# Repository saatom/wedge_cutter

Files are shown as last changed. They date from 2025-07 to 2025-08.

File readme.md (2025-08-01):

# readme
Created by Wyatt Richards <wr1701@proton.me>

beta branch

Made during my time working at Great Land Window.

This is a dispenser for _TREMCO POLYSHIM II_ window wedge (specifically the 0.160" size). It is designed to work with a NEMA 23 closed-loop stepper motor with approximately 3.0 Nm of maximum output torque. Bearings are standard 802 22mm OD/ 8mm ID ones with a smaller bearing on the giullotine assembly specified as having 7mm OD / 3mm ID.

Oversized holes are for machine screw heat-set inserts (M3 and M4 sizes) with three pockets for M5 nuts on the motor housing assembly.

Electrical diagram(s) for this machine are not provided but are pretty straight forward. It is designed to use 20 vdc input from Dewalt brand batteries, which is split into three different voltages and are as follows:
* 20 to 35 vdc step up module for 35 vdc input to the stepper driver
* 7 vdc regulator for servo power
* 5 vdc for Raspberry PI Pico input (note that the RPI has an internal voltage regulator that brings it down to 3.3 vdc, thus all logic and LEDs are running on 3.3 volts and not 5)

Pin configurations are designed for ease of assembly and maintenance and are hard-coded into the .ino file, which is compiled using the standard arduino-cli package for Linux and uploaded manually to the RPI.

Please consult the instruction manual with questions, otherwise you can email me at the aforementioned address.



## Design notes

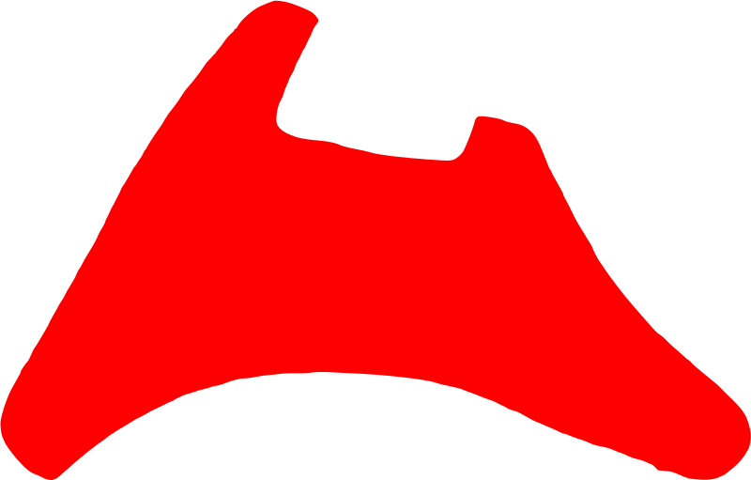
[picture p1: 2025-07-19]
Cutter_Profile2.png

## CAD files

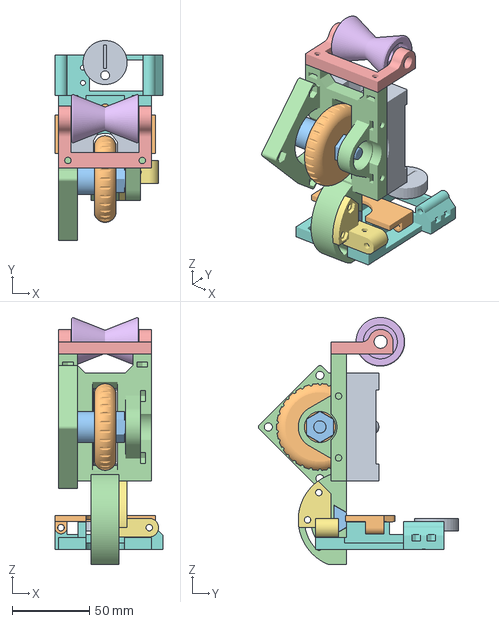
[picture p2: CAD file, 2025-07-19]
3d_print_files/Wedge Cutter Assembly V3_2.3mf
70.0 x 129.2 x 159.5 mm

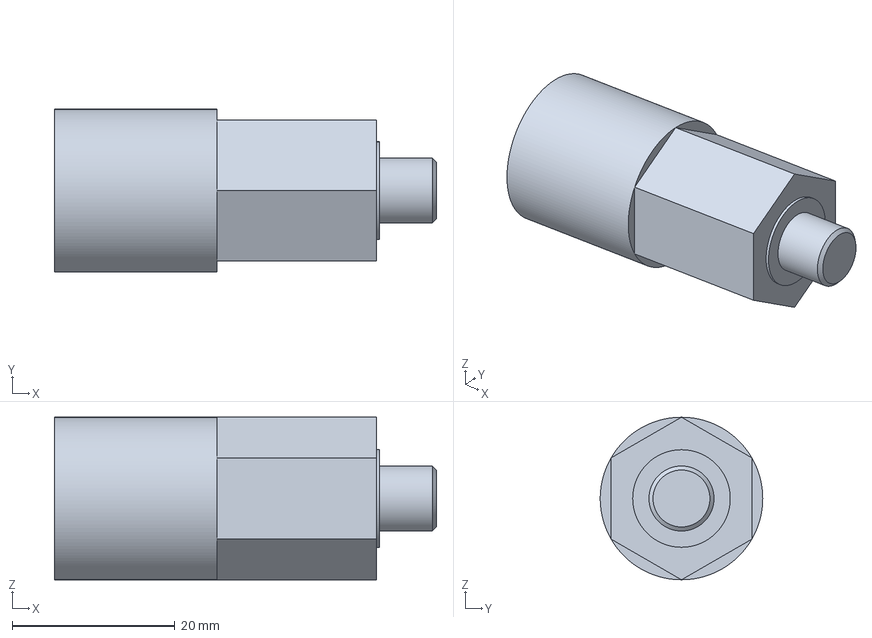
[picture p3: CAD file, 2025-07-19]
3d_print_files/Axle V2.3mf
47.0 x 20.0 x 20.0 mm

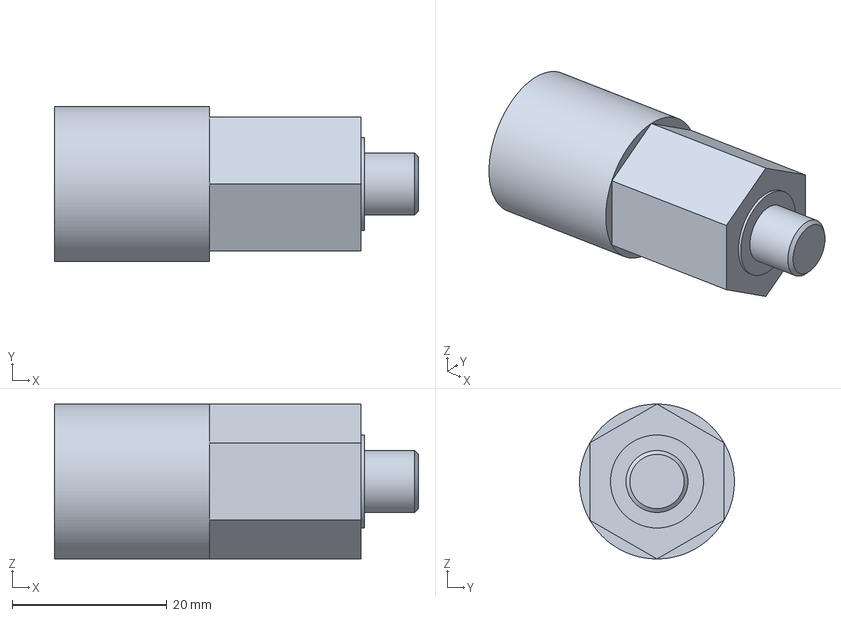
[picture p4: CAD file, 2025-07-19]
3d_print_files/AxleWithCutout.3mf
47.0 x 20.0 x 20.0 mm

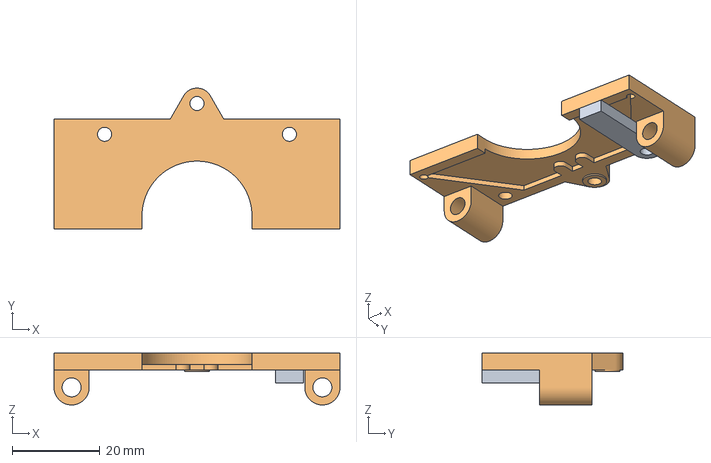
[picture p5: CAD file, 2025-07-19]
3d_print_files/Blade Parts V3.3mf
65.0 x 32.0 x 11.8 mm

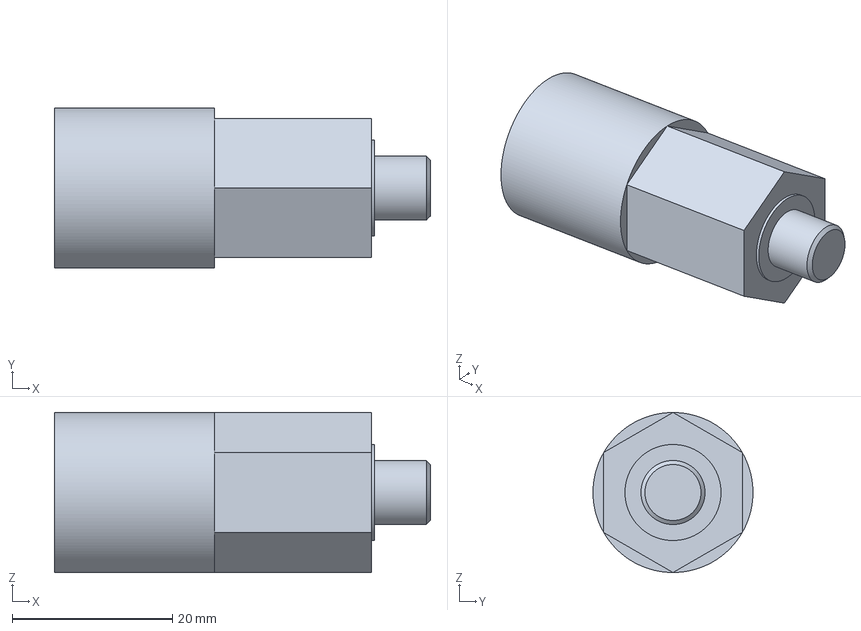
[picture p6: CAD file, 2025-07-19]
3d_print_files/Axle.3mf
47.0 x 20.0 x 20.0 mm

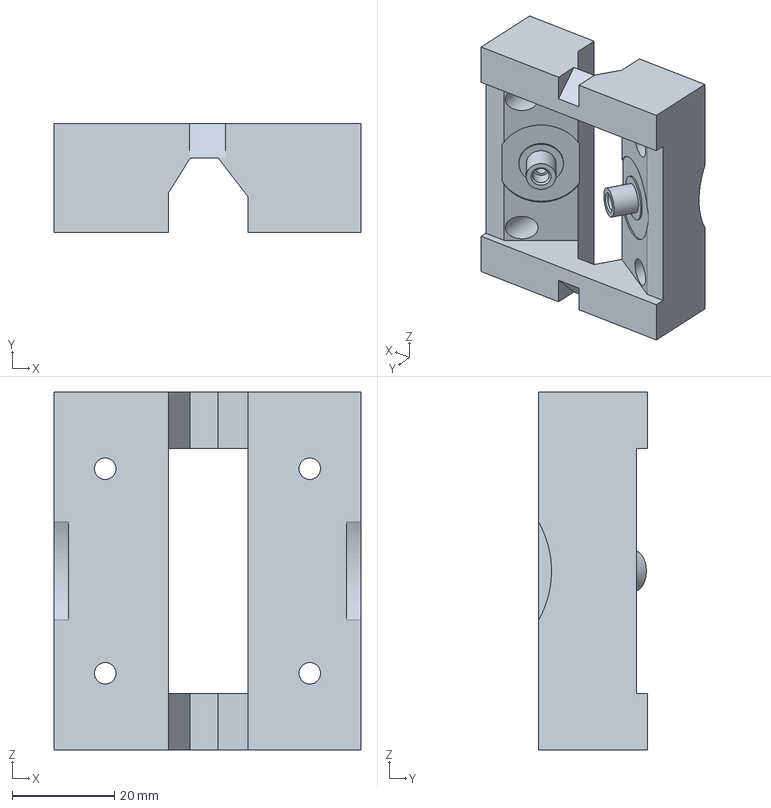
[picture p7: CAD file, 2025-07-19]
3d_print_files/Guide V3_2.3mf
60.0 x 21.2 x 70.0 mm

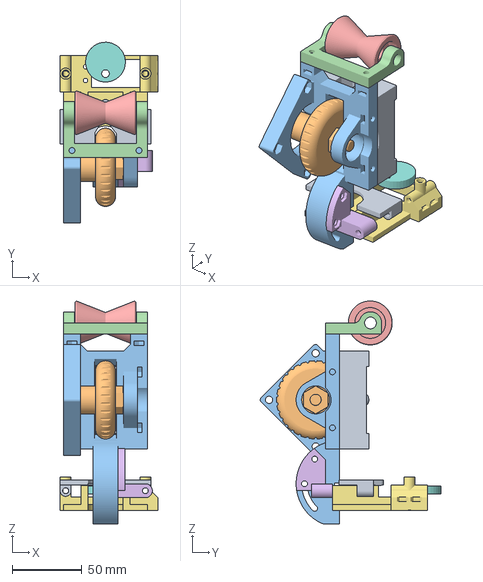
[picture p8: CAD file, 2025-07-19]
3d_print_files/Wedge Cutter V3_1 Core.3mf
70.0 x 129.2 x 159.5 mm

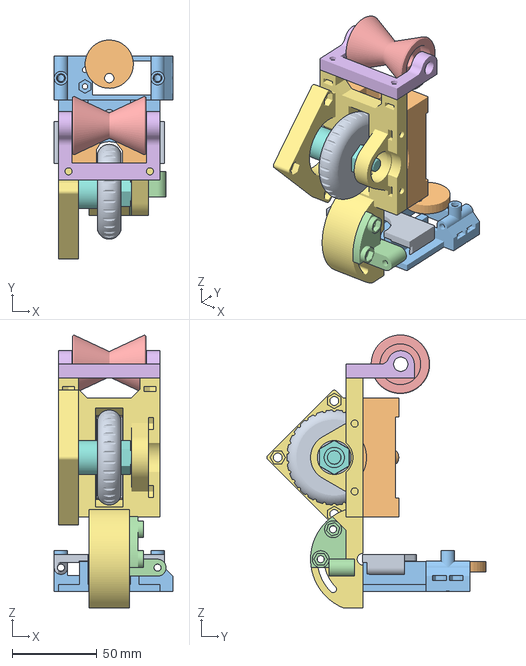
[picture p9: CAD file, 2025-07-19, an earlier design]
3d_print_files/Wedge Cutter Assembly V3.3mf
70.0 x 129.2 x 161.0 mm

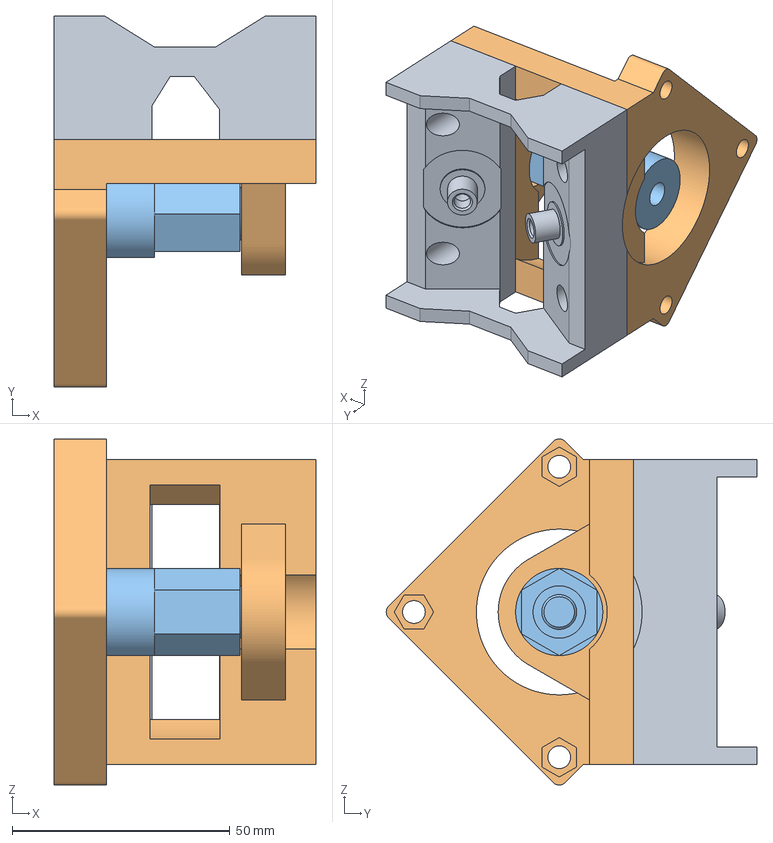
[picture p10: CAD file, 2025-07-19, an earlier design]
3d_print_files/Wedge Cutter V3 Core.3mf
60.0 x 85.0 x 79.4 mm

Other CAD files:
3d_print_files/Guide V3.3mf

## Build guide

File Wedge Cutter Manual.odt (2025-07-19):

WEDGE DISPENSER

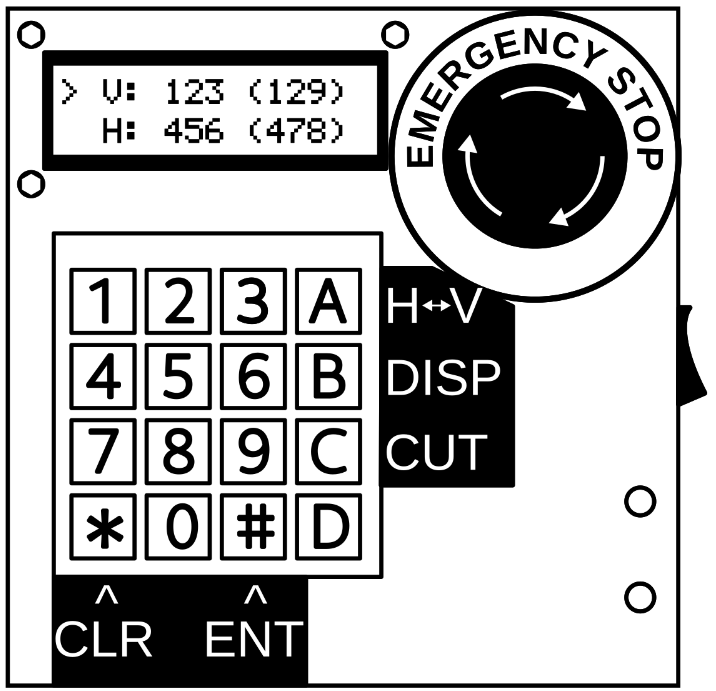
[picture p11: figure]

MADE BY WYATT RICHARDS

# User Interface

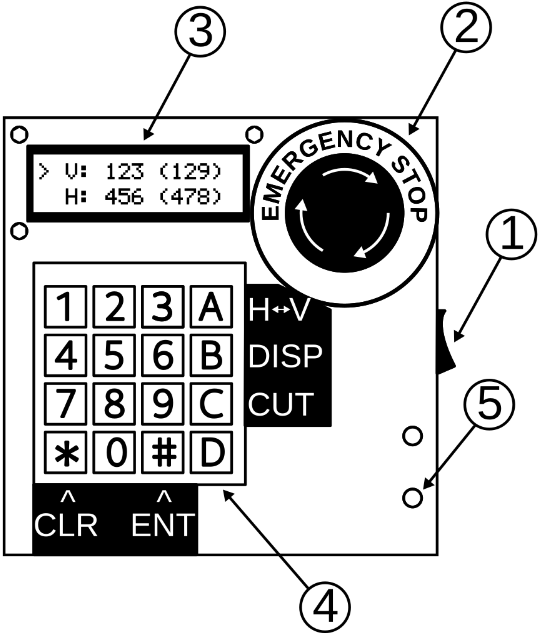
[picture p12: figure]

USER INTERFACE KEY
1 | Main power switch
2 | Emergency stop
3 | LCD
4 | Keypad
5 | Power indication light

# Operation

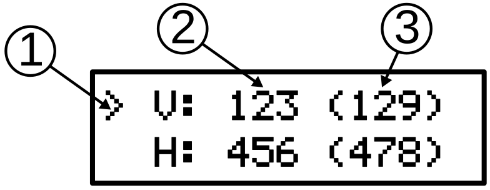
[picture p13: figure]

OPERATION KEY
1 | Line indicator
2 | Glass dimension (mm)
3 | Actual dispense dimension (mm)

## Operation instructions

1. Press “A” on keypad to switch between V (vertical) and H (horizontal) dimension
  a. The carat (1) indicates which dimension is currently selected
2. Input the glass dimension in millimeters
  a. The glass dimension (2) will be displayed with underscores (e.g. __12) to indicate input mode
3. Press “#” on keypad to enter dimension
  a. 4-digit dimensions will automatically enter when the fourth digit is input
  b. The actual glass dimension (3) will automatically update
  c. Pressing “*” on keypad will clear all current digits

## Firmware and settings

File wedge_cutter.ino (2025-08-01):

#include <LiquidCrystal.h>
#include <math.h>
#include <Servo.h>
#include "AccelStepper.h"
#include <EEPROM.h>
#include <string>
#include <iostream>

#include "pico/stdlib.h"
#include "pico/flash.h"
using namespace std;

#define dirPin 10  //stepper setup
#define stepPin 9
#define stepsPerRevolution 1600
#define servoPin 14
#define wedgeMultiplier 1.017  //1.016  //amount to lengthen the wedge by
#define wedgeOffset 27         //27 //offset from original glass dimension
#define estopPin 28
#define enaPin 12
#define almPin 11


Servo myservo;
AccelStepper stepper = AccelStepper(1, stepPin, dirPin);

unsigned long stepperPos = 0;

//end stepper and servo setup
const int rs = 16, en = 17, d4 = 18, d5 = 19, d6 = 20, d7 = 21;  //lcd setup
LiquidCrystal lcd(rs, en, d4, d5, d6, d7);

int cols[4] = { 7, 6, 5, 4 };  //keypad setup
int rows[4] = { 3, 2, 1, 0 };

int vals[2] = { 0, 0 };      //length values stored for dispensing
int tempvals[2] = { 0, 0 };  //length values displayed on screen
int qty = 1;
int pos = 0;            //cursor position; 0 is top, 1 is bottom row of LCD
int keydeb = 0;         //debounce for key press
int keyDelay = 100;     //debounce delay on keypad in milliseconds
int chr[2] = { 0, 0 };  //which digit the input is on; e.g. chr[0] = 2 means that the next input is the hundreds place on the first row
int lastKey = -1;
int calMem = 0;  //EEPROM memory address of calibration number
double magicNumber = 1.0;
int mode = 0;  //Starts in normal mode

int keymap[4][4] = {  //mapping the keypad matrix to its associated buttons; 0-9 are raw inputs, 10-15 are used for special functions
  { 1, 2, 3, 12 },
  { 4, 5, 6, 13 },
  { 7, 8, 9, 14 },
  { 10, 0, 11, 15 }
};

double offset(double mm) {
  if (mm < 27) {
    return 0;
  } else {
    return (mm - wedgeOffset) * wedgeMultiplier;
  }
}

int digits(int value) {
  int dig = 1;
  while (floor((double)value / (pow(10, double(dig)))) > 0) {
    dig = dig + 1;
  }
  return dig;
}

void checkEstop() {
  int estop = digitalRead(estopPin);
  if (estop == LOW) {
    lcd.clear();
    lcd.setCursor(1, 0);
    lcd.print("RELEASE E-STOP");
    unsigned long last = millis();
    //int i = 0;
    do {
      delay(50);
    } while (millis() - 5000 < last && digitalRead(estopPin) == LOW);
    if (digitalRead(estopPin) == HIGH) {
      lcd.clear();
      lcd.setCursor(1, 0);
      lcd.print("RESUMING IN 2");
      delay(1000);
      lcd.clear();
      lcd.setCursor(1, 0);
      lcd.print("RESUMING IN 1");
      delay(1000);
    }
  }
}

void updateLCD() {
  int vdig = digits(tempvals[0]);
  int hdig = digits(tempvals[1]);
  int vact = offset(vals[0]);
  int hact = offset(vals[1]);
  int vdigact = digits(vact);
  int hdigact = digits(hact);

  lcd.setCursor(0, pos);
  lcd.print(">");
  lcd.setCursor(0, 1 - pos);
  lcd.print(" ");

  lcd.setCursor(1, 0);
  lcd.print(" V: ");
  for (int i = 0; i < 4 - vdig; i++) {
    if (chr[0] < 1) {
      lcd.print(" ");
    } else {
      lcd.print(" ");
    }
  }

  lcd.print(tempvals[0]);
  lcd.print(" (");
  //lcd.print(static_cast<int>(vals[0] * wedgeMultiplier));
  lcd.print(static_cast<int>(vact));
  lcd.print(")");
  for (int i = 0; i < 4 - vdigact; i++) {
    lcd.print(" ");
  }

  lcd.setCursor(1, 1);
  lcd.print(" H: ");
  for (int i = 0; i < 4 - hdig; i++) {
    if (chr[1] < 1) {
      lcd.print(" ");
    } else {
      //lcd.print("_");
      lcd.print(" ");
    }
  }

  lcd.print(tempvals[1]);
  lcd.print(" (");
  //lcd.print(static_cast<int>(vals[1] * wedgeMultiplier));
  lcd.print(static_cast<int>(hact));
  lcd.print(")");
  for (int i = 0; i < 4 - hdigact; i++) {
    lcd.print(" ");
  }
}

void dispense(double mm) {  //dispenses the wedge
  int val = mm / (2.0 * 3.1415926 * 28.0) * static_cast<double>(stepsPerRevolution) * magicNumber;
  stepper.setCurrentPosition(0);
  //stepperPos = stepperPos + val;
  //stepper.moveTo(stepperPos);
  stepper.moveTo(val);
  stepper.runToPosition();
  //stepper.runToNewPosition();
}

double retLength = 4;  //amount to retract wedge when cutting in millimters

void cut() {  //chops the wedge
  checkEstop();
  //lcd.clear();
  //updateLCD();
  myservo.write(180);
  delay(1200);
  myservo.write(0);
  dispense(-retLength);  //retract wedge a bit to prevent it from catching on the blade on the way up
  delay(500);
  dispense(retLength);
}

void setup() {
  Serial.begin(9600);
  EEPROM.begin(512);

  //EEPROM.write(calMem, 100);
  magicNumber = EEPROM.read(calMem)/100.0;

  myservo.attach(servoPin, 400, 2600);  //servo and stepper initialization
  stepper.setMaxSpeed(4000);
  stepper.setAcceleration(3200);  //stepper acceleration value
  stepper.setCurrentPosition(0);
  //stepper.setEnablePin(enaPin);
  myservo.write(0);
  pinMode(enaPin, OUTPUT);
  //digitalWrite(enaPin, HIGH);
  digitalWrite(enaPin, LOW);
  //pinMode(servoPin, OUTPUT);

  lcd.begin(16, 2);
  //lcd.cursor();
  pinMode(estopPin, INPUT_PULLUP);
  for (int i = 0; i < 4; i++) {
    pinMode(rows[i], OUTPUT);
    pinMode(cols[i], INPUT_PULLUP);
    //digitalWrite(cols[i], HIGH);
  }
  lcd.setCursor(4, 0);
  lcd.print("Welcome");
  lcd.setCursor(0, 1);
  lcd.print("Sw. Version 2.01");

  delay(3000);
  lcd.clear();
  updateLCD();
}

void enterLine() {
  qty = 1;
  vals[pos] = tempvals[pos];
  //chr[pos] = 0;
  updateLCD();
  Serial.println("Enter");
}

void clearLine() {
  //tempvals[pos] = vals[pos];
  tempvals[pos] = 0;
  chr[pos] = 0;
  enterLine();
  updateLCD();
  Serial.println("Clear");
}

void addNum(int number) {
  if (chr[pos] > 3) {
    chr[pos] = 0;
    tempvals[pos] = 0;
  } else if (chr[pos] == 0) {
    tempvals[pos] = 0;
  }
  tempvals[pos] = tempvals[pos] * 10 + number;

  Serial.println(tempvals[pos]);
  if (chr[pos] == 4) {
    //enterLine();
    clearLine();
  } else {
    chr[pos] = chr[pos] + 1;
  }
  enterLine();
  updateLCD();
}

int getKey() {
  //int pressed = 0;
  int key = -1;
  for (int i = 0; i < 4; i++) {
    digitalWrite(rows[i], LOW);
    for (int v = 0; v < 4; v++) {
      int val = digitalRead(cols[v]);
      if (val == LOW) {
        //pressed = pressed + 1;
        key = keymap[v][i];
        break;
      }
      if (key > -1) {
        break;
      }
    }
    digitalWrite(rows[i], HIGH);
  }
  if (keydeb + keyDelay < millis() && key != lastKey) {
    keydeb = millis() + keyDelay;
    lastKey = key;
    return key;
  } else {
    lastKey = key;
    return -1;
  }
}

int calibrate() {
  lcd.clear();
  lcd.setCursor(0, 0);
  lcd.print("Calibration ");
  magicNumber = EEPROM.read(calMem)/100.0;
  lcd.print(magicNumber);
  lcd.setCursor(0,1);
  lcd.print("Press # to cont.");
  unsigned long startedMill = millis();
  while(1==1){
    int key = getKey();
    if(key == 11){
      break;
    }
    else if(key == 10 || millis() > startedMill + 5000){
      updateLCD();
      return 0;
    }
    delay(50);
  }
  lcd.clear();
  lcd.setCursor(2,0);
  lcd.print("Disp. Sample");

  dispense(125.0);
  cut();
  lcd.clear();
  lcd.setCursor(1, 0);
  lcd.print("Input Length:");
  lcd.setCursor(6, 1);
  //numstr=to_string(magicNumber);
  int chars = 3;
  int newval = 0;
  for(int i=0; i<chars; i++) {
    while(1==1) {
      int key = getKey();
      if(key > -1 && key < 10){ //number input
        newval = newval + key*pow(10,(2-i));
        lcd.print(key);
        break;
      }
      else if(key == 10) { //cancel
        updateLCD();
        return 0;
      }
    }
  }
  magicNumber = (125.0/static_cast<int>(newval))*magicNumber;
  EEPROM.write(calMem, ceil(magicNumber*100.0));
  EEPROM.commit();
  lcd.clear();
  lcd.setCursor(0,0);
  lcd.print("Set cal to ");
  lcd.print(magicNumber);
  delay(2000);
  updateLCD();
  return 1;
}

void loop() {
  int key = getKey();
  if (key > -1 && key < 10) {  //normal number input
    Serial.println(key);
    addNum(key);
  } else if (key == 12) {  //swap line button
    Serial.println("A");
    chr[pos] = 0;
    vals[pos] = tempvals[pos];
    pos = 1 - pos;
    updateLCD();
  } else if (key == 14) {  //cut button
    Serial.println("C");
    //digitalWrite(enaPin, LOW);
    delay(200);
    cut();
    //digitalWrite(enaPin, HIGH);
  } else if (key == 13) {  //dispense button
    checkEstop();
    if (digitalRead(estopPin) == HIGH) {
      lcd.clear();
      lcd.setCursor(3, 0);
      lcd.print("DISPENSING");
      lcd.setCursor(4, 1);
      lcd.print("QTY: ");
      lcd.print(qty);
      //digitalWrite(enaPin, LOW);
      //delay(800);
      dispense(offset(vals[0]));
      cut();
      dispense(offset(vals[0]));
      cut();
      dispense(offset(vals[1]));
      cut();
      dispense(offset(vals[1]));
      cut();
      //digitalWrite(enaPin, HIGH);
      qty = qty + 1;
    }
    lcd.clear();
    updateLCD();
  } else if (key == 11) {  //Menu button
    //enterLine();
    calibrate();
  } else if (key == 10) {  //clear button
    clearLine();
  } else if (key == 15) {  //single dispense button
    checkEstop();
    if (digitalRead(estopPin) == HIGH) {
      lcd.clear();
      lcd.setCursor(3, 0);
      lcd.print("DISPENSING");
      lcd.setCursor(4, 1);
      lcd.print("SINGLE ");
      if (pos == 0) {
        lcd.print("V");
      } else {
        lcd.print("H");
      }
      //digitalWrite(enaPin, LOW);
      //delay(800);
      dispense(offset(vals[pos]));
      cut();
    }
    lcd.clear();
    updateLCD();
  }
}

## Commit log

2025-07-31 Added calibration key and adjusted key pressed methods
2025-07-31 Improved calibrate UI
